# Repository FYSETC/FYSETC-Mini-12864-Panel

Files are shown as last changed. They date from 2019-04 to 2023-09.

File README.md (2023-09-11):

# Mini-12864-Panel

## Product Introduction

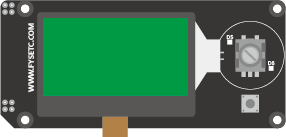
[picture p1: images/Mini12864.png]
Mini12864


这是一个便宜，带RGB指示灯，通用于marlin的显示屏，支持脱机打印，分辨率为12864，显示区域为2.4’‘，SD卡座可以为侧式或者立式，方便不同的安装场合，非常适用于小型3D打印机。

This is a opensouce, cheap, with RGB indicator, common to marlin's display, supports offline printing, resolution is 12864, display area is 2.4'', SD card holder can be side or vertical, convenient for different installation occasions Ideal for small 3D printers.

There are two versions, one with only two RGB LEDs around the encoder, the backlight is fixed color; the other one backlight is also RGB.

## Features

- 2.4" inch high contrast Graphic LCD
- Black-gray/black-green/white-black/white-blue/green-black, 5 display styles
- SPI communication to host micro-controller
- Support Vertical or side SD slot with card detect
- Rotary Encoder 
- Configurable RGB LED light
- Software configurable contrast setting
- 3D printable case and mount STL file 
- EXP1 & EXP2  RAMPS Compatible socket

## Application

3D printer，CNC machines ，Other micro controller projects

## Typical  Wiring






## 注意/NOTICE：

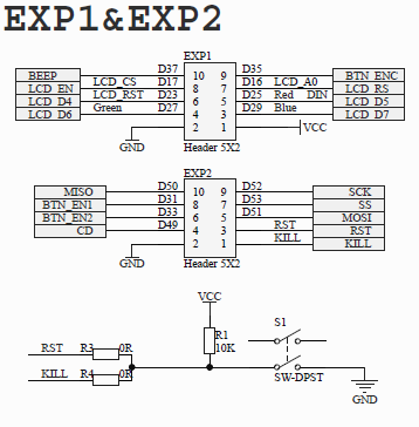
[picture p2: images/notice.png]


| Notice                                                       |
| ------------------------------------------------------------ |
| 为了兼容某些主板，如RAMPS1.4，FYSETC mini12864 设置了 RST(R3) 和 KILL(R4) 的可选择电阻。目前，有些主板（S6/Spider）将 KILL 换成 5V，此时，请确认 mini12864 上 R4处于空贴状态，否则按下屏幕上的按钮会致使 5V 与 GND 短路，长时间操作会导致主板损坏。<br/>   In order to be compatible with some motherboards, such as RAMPS1.4, mini12864 is equipped with RST (R3) and KILL (R4) optional resistors. At present, some motherboards (S6/Spider) change the KILL to 5V. At this time, please make sure that R4 on the mini12864 is in the empty state, otherwise pressing the button on the screen will cause a short circuit between 5V and GND, and long-term operation will cause the motherboard to be damaged. |

## Firmware config

### Marlin

Uncomment the following define according to your panel version, you can check it at the back of the panel.

```
//
// FYSETC variant of the MINI12864 graphic controller with SD support
// https://wiki.fysetc.com/Mini12864_Panel/
//
//#define FYSETC_MINI_12864_X_X    // Type C/D/E/F. No tunable RGB Backlight by default
//#define FYSETC_MINI_12864_1_2    // Type C/D/E/F. Simple RGB Backlight (always on)
//#define FYSETC_MINI_12864_2_0    // Type A/B. Discreet RGB Backlight
//#define FYSETC_MINI_12864_2_1  // Type A/B. Neopixel RGB Backlight
//#define FYSETC_GENERIC_12864_1_1 // Larger display with basic ON/OFF backlight.
```

### Klipper on Cheetah V3.0

```
[display]
#	mini12864 LCD Display
lcd_type: uc1701
cs_pin: PB15
a0_pin: PB12
rst_pin: PB13
encoder_pins: ^PC10,^PC11
click_pin: ^!PC6
contrast: 63
#spi_bus: spi1
spi_software_mosi_pin: PA7
spi_software_miso_pin: PA6
spi_software_sclk_pin: PA5

[neopixel fysetc_mini12864]
#	To control Neopixel RGB in mini12864 display
pin: PB14
chain_count: 3
initial_RED: 0.1
initial_GREEN: 0.5
initial_BLUE: 0.0
color_order: RGB

#	Set RGB values on boot up for each Neopixel. 
#	Index 1 = display, Index 2 and 3 = Knob
[delayed_gcode setdisplayneopixel]
initial_duration: 1
gcode:
        SET_LED LED=fysetc_mini12864 RED=1 GREEN=1 BLUE=1 INDEX=1 TRANSMIT=0
        SET_LED LED=fysetc_mini12864 RED=1 GREEN=0 BLUE=0 INDEX=2 TRANSMIT=0
        SET_LED LED=fysetc_mini12864 RED=1 GREEN=0 BLUE=0 INDEX=3 
```

## Attention

-TBD-

## FAQ

-TBD-

## Attachments
### 1. Schematic

---------

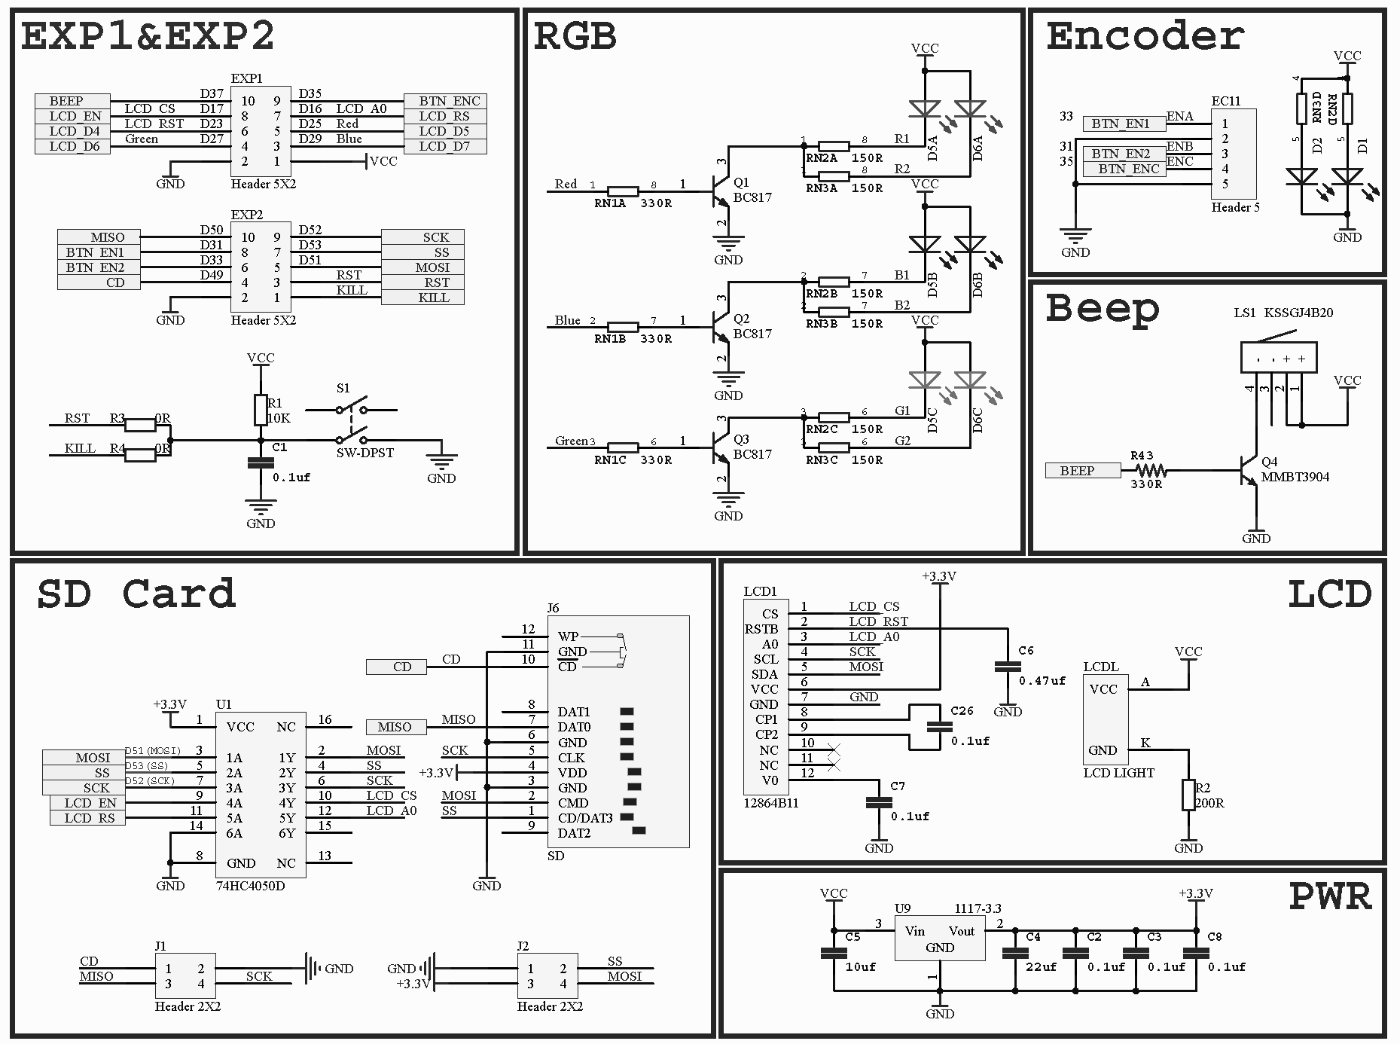
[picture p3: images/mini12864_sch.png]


### 2. Dimensions

---------

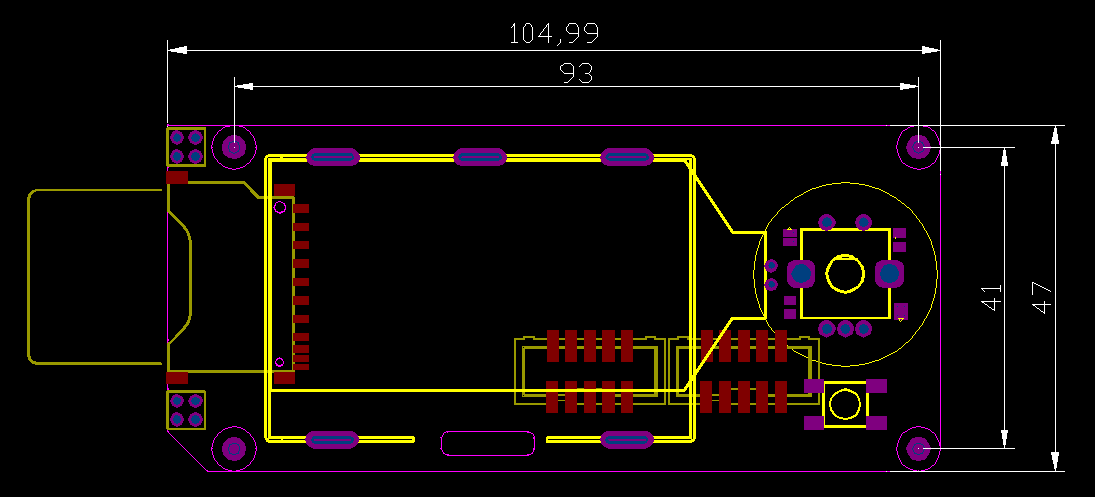
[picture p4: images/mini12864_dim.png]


**For detailed dimensions please check dwg/step file on github.**

## Shop
---
- [LCD](  )

## Tech Support
---
Please submit any technical issue into our [forum](http://forum.fysetc.com/) 

```

```

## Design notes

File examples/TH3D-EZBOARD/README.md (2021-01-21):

# FYSETC Mini 12864 Panel

FYSETC Mini 12864 Panel EXP1 and EXP2:

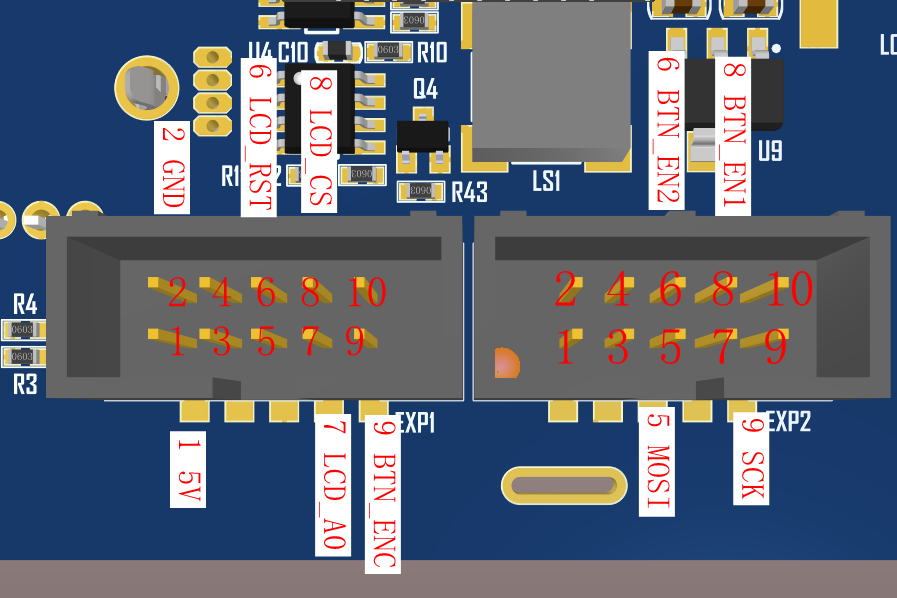
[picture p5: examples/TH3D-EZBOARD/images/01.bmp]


TH3D EZBoard EXP1:

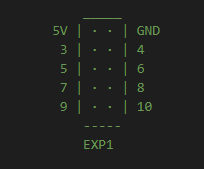
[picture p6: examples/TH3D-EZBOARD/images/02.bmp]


TH3D EZBoard only supports CR10_STOCKDISPLAY,If you want to support FYSETC Mini 12864 Panel, you need to carry out the flying line operation, so you need to prepare 10 Dupont lines, the connection operation is as follows:

| FYSETC Mini 12864 Panel EXP1 and EXP2 | TH3D EZBoard EXP1 |
| --- | --- |
| 5V | 1 |
| GND | 2 |
| LCD_CS | 3 |
| LCD_A0 | 4 |
| MOSI | 5 |
| EN2 | 6 |
| LCD_RST | 7 |
| EN1 | 8 |
| ENC | 9 |
| SCK | 10 |

## Firmware config

This firmware is only used to test mini12864, if you want to support on the latest Marlin firmware, you need to configure the following

##### Step1. changes the pins.

On a TH3D_EZBOARD board, you need to make the following changes in pins_TH3D_EZBOARD.h:

```cpp tab='pins_TH3D_EZBOARD.h'
// #if ENABLED(CR10_STOCKDISPLAY)
//   #define BEEPER_PIN                       P1_31
//   #define BTN_EN1                          P3_26
//   #define BTN_EN2                          P3_25
//   #define BTN_ENC                          P1_30
//   #define LCD_PINS_RS                      P0_16
//   #define LCD_PINS_ENABLE                  P0_18
//   #define LCD_PINS_D4                      P0_15
//   #define KILL_PIN                         P2_11
// #elif HAS_SPI_LCD
//   #error "Only the CR10_STOCKDISPLAY is supported with TH3D EZBoard."
// #endif

#if ENABLED(CR10_STOCKDISPLAY)
  #define BEEPER_PIN                       P1_31
  #define BTN_EN1                          P3_26
  #define BTN_EN2                          P3_25
  #define BTN_ENC                          P1_30
  #define LCD_PINS_RS                      P0_16
  #define LCD_PINS_ENABLE                  P0_18
  #define LCD_PINS_D4                      P0_15
  #define KILL_PIN                         P2_11
#elif ENABLED(FYSETC_MINI_12864)

  #define BTN_EN1                         P3_26
  #define BTN_EN2                         P3_25
  #define BTN_ENC                         P1_30

  #define DOGLCD_CS                       P0_18
  #define DOGLCD_A0                       P0_16
  #define DOGLCD_SCK                      P1_31
  #define DOGLCD_MOSI                     P0_15
  #define LCD_PINS_ENABLE                 P0_18
  #define LCD_PINS_RS                     P0_16

  #define FORCE_SOFT_SPI

  #define LCD_RESET_PIN                   P2_11

#elif HAS_SPI_LCD
  #error "Only the CR10_STOCKDISPLAY is supported with TH3D EZBoard."
#endif
```

##### Step2. Config the configuration.h.

Because the TH3D_EZBOARD board has only EXP1 interface, it will not be able to use the RGB function

```C++
#define FYSETC_MINI_12864_X_X    // Type C/D/E/F. No tunable RGB Backlight by default
//#define FYSETC_MINI_12864_1_2    // Type C/D/E/F. Simple RGB Backlight (always on)
//#define FYSETC_MINI_12864_2_0    // Type A/B. Discreet RGB Backlight
//#define FYSETC_MINI_12864_2_1    // Type A/B. NeoPixel RGB Backlight
//#define FYSETC_GENERIC_12864_1_1 // Larger display with basic ON/OFF backlight.
```

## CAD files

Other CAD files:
hardware/V2.1/12864mini（RGB）_V2.1.DWG
hardware/V1.2/12864mini_V1.2.DWG
hardware/V2.0/12864mini（RGB）_V2.0.DWG

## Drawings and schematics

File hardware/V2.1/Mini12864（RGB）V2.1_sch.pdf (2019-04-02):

# Encoder

EXP1&EXP2 | RGB

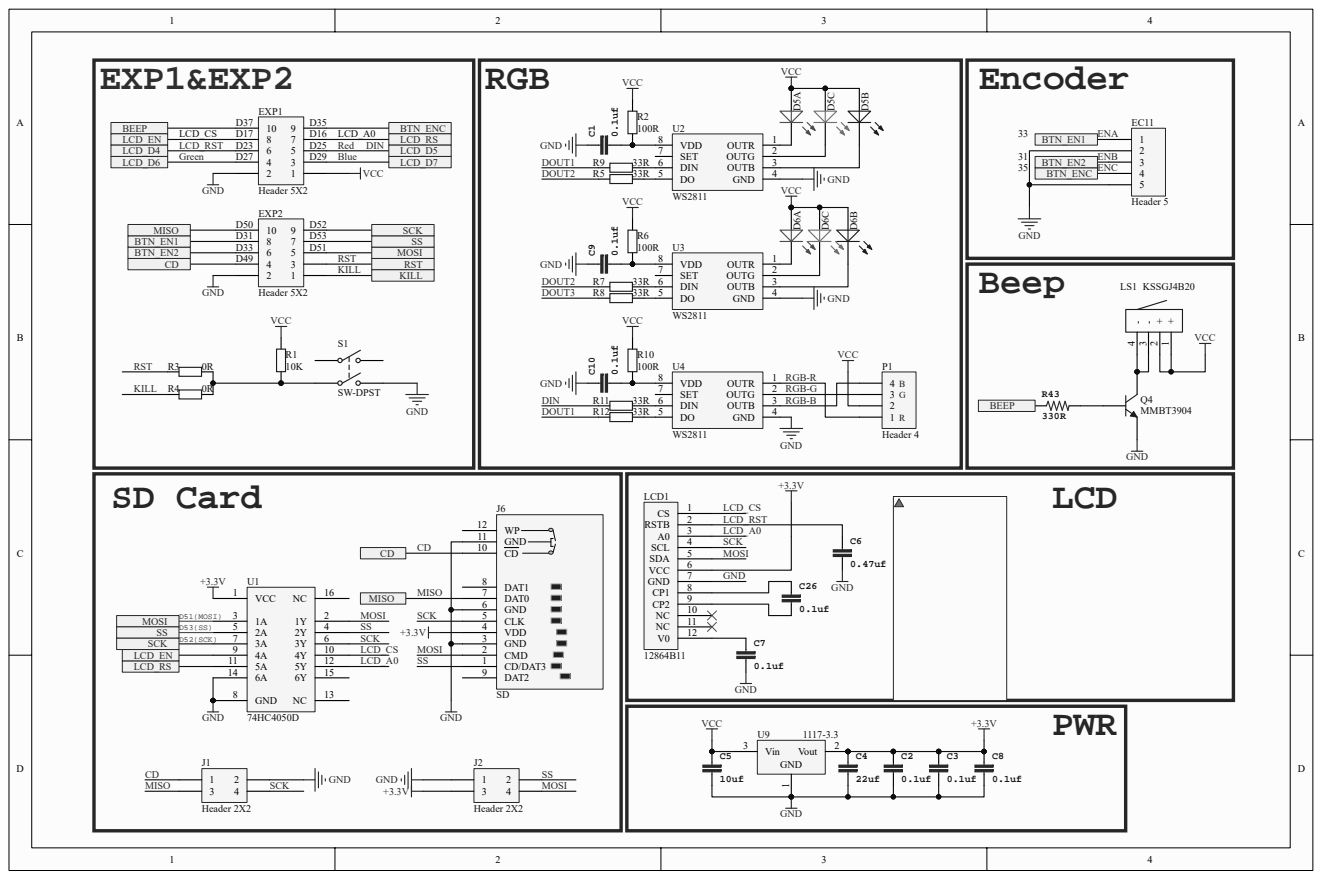
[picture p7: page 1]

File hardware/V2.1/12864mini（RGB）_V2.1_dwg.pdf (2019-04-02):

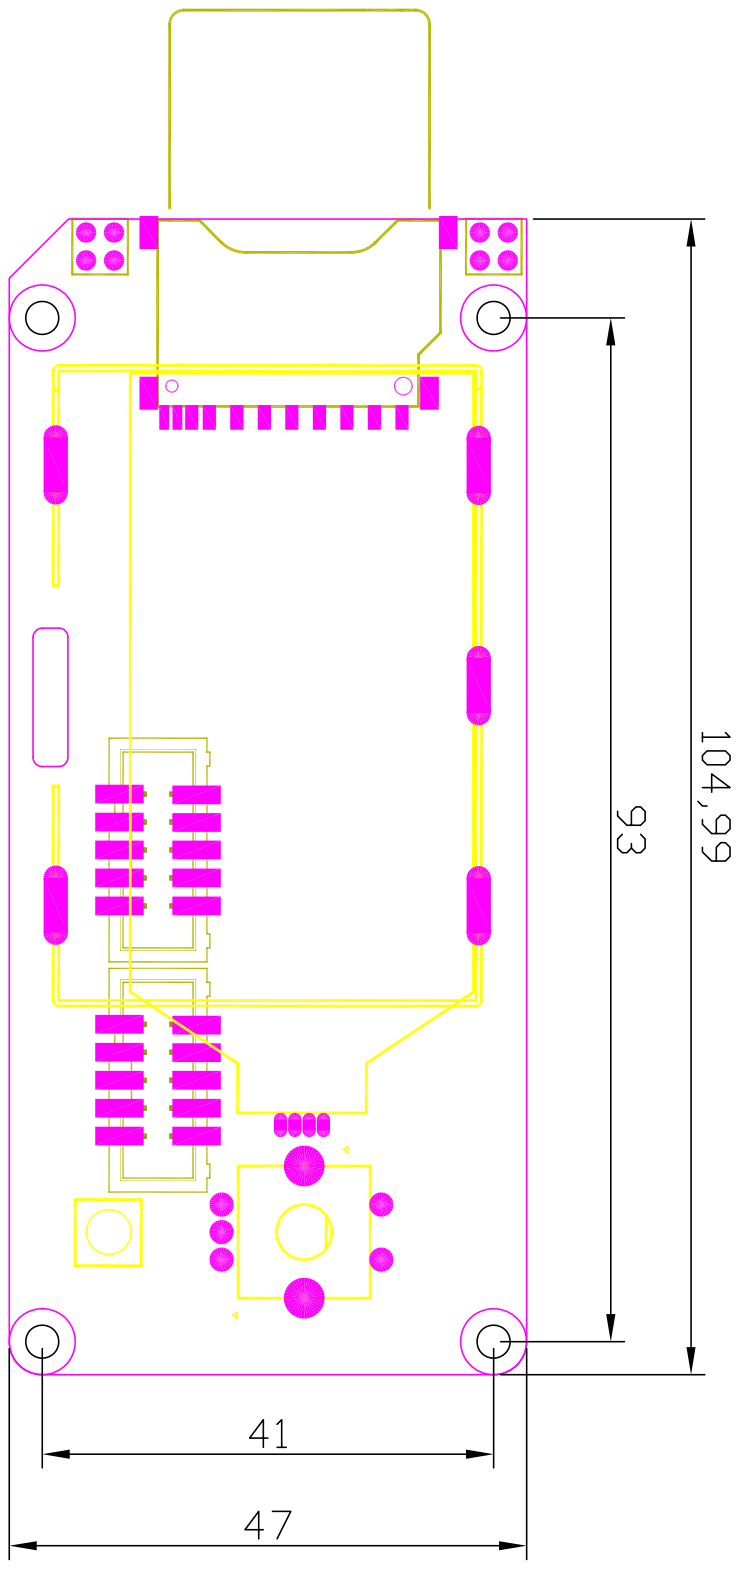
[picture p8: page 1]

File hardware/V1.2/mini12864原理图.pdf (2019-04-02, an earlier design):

# Encoder

EXP1&EXP2 | RGB

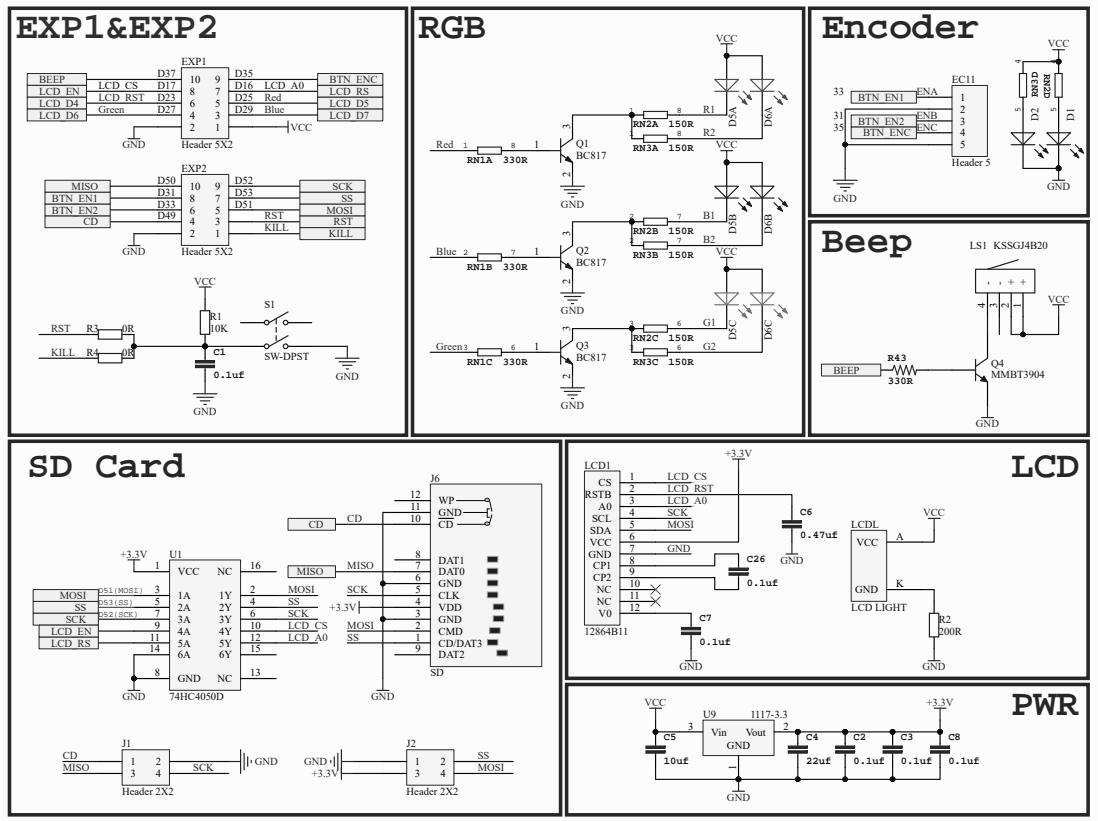
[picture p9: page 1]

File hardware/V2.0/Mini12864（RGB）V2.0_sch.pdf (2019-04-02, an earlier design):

# Encoder

EXP1&EXP2 | RGB

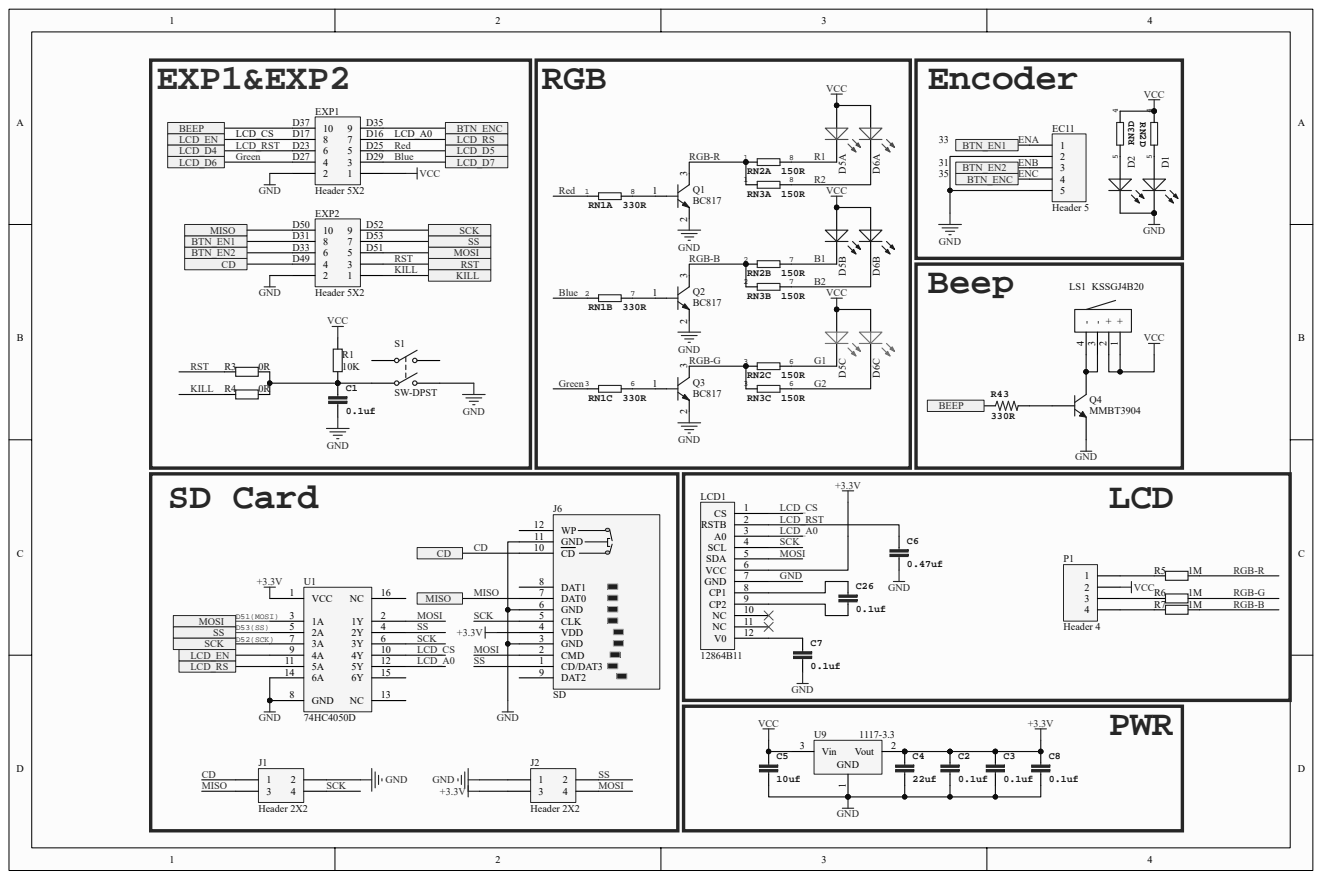
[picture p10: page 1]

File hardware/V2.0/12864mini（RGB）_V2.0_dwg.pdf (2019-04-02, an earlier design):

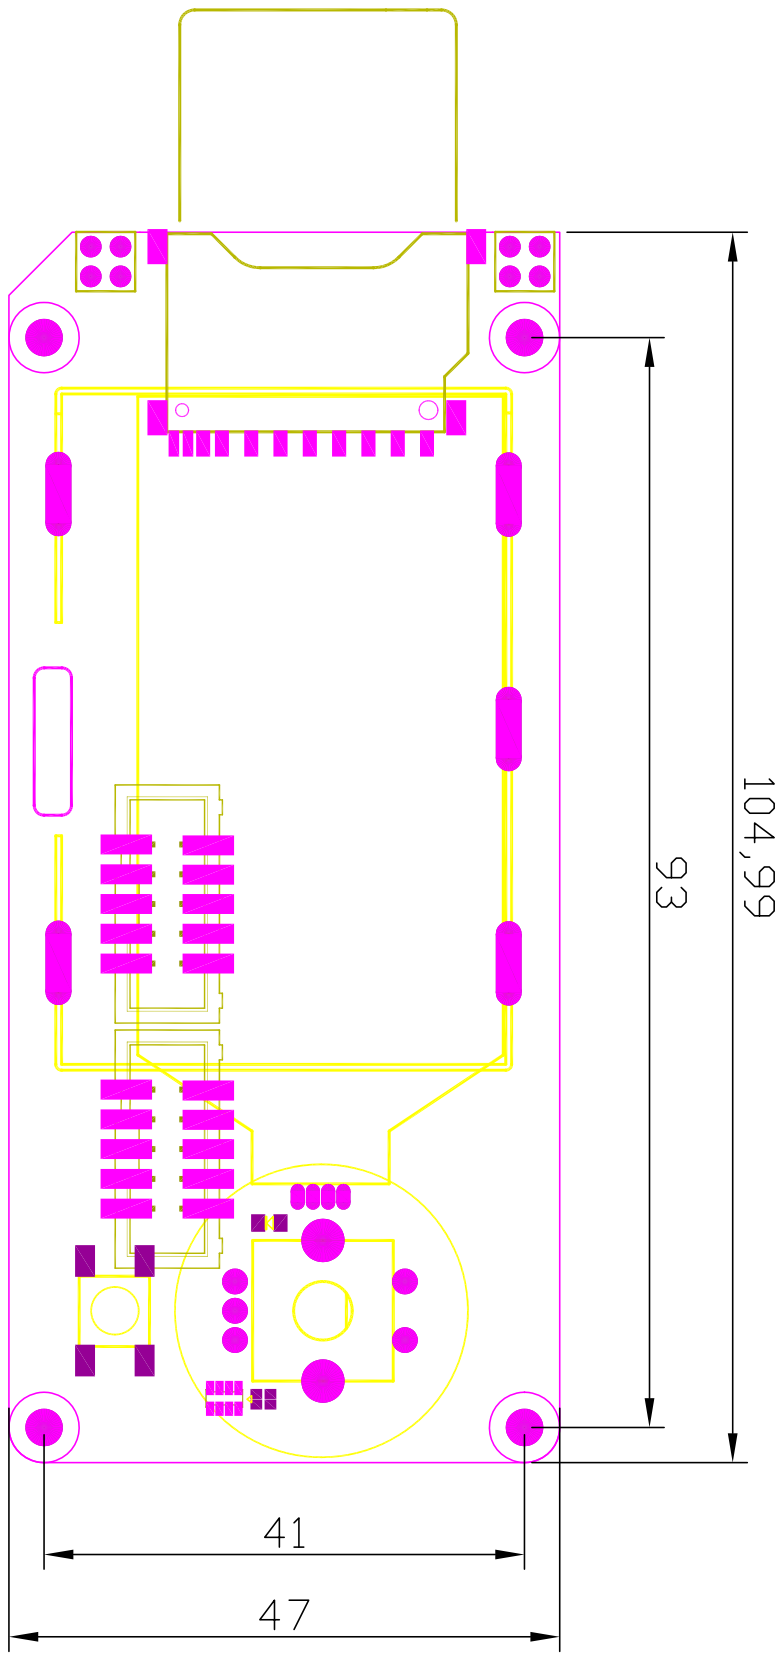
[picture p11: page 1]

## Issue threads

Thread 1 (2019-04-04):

Display does not work

Brainc0re, 2019-04-04:
I have a CR10S-Pro which normally use a touchscreen. But i didn't like and replaced it with a 12864 reprap full graphic controller. That controller/display works since weeks. So i thought, that this mini12864 will work too. But im not able to run it :/ Not even the backlight works (Pin1 and Pin2 are correct - i can meassure 5V - Pin1 (+) // Pin2 (-) and J2 has 3.3V)
I made the changes in Marlin which are provided by fysetc on their website.

Is it possible, that this display wont work on the creality mainboard?

Current Firmware (reprap 12864): https://drive.google.com/open?id=1HoQVlum-DM5lGhCuu1yqCfW6UupuqbK6
FW for mini12864: https://drive.google.com/open?id=11KdF0nT0fa-EBrvGuiYhUTILRo4qJgjR
Mainboard layout: https://drive.google.com/open?id=1Ya5zHF_WQpw7XY_BoL0zs20UwexBvtwI

Attention: Both FWs has the same *.ino name but different folder names.

ejhoness, 2021-12-17:
180º EXP1 and EXP2 in lcd,

Eugeniusz-Gienek, 2024-03-12:
> 180º EXP1 and EXP2 in lcd,

OMG that worked! Thanks man!

Closed 2024-09-19.

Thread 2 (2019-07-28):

STEP files for display are corrupted

eddietheengineer, 2019-07-28:
I am making an enclosure for this display, but the STEP files included in the Github links will not open. Can you check the files and reupload them?

Thanks!

jonathanlundstrom, 2019-09-08:
I've been at this for months and still haven't been able to use these files. The LCD mount is one of the last things on my to-do in order to finish my machine and I have not been able to design it properly. Please upload new files!

danym21, 2019-09-17:
looks like some one has changed the step files to a .zip file with a link to a
Potentially Unwanted Application (PUA)
https://www.f-secure.com/sw-desc/pua.shtml
please replace it with the correct files!!

jonathanlundstrom, 2019-09-17:
I got the correct file from a guy on their Facebook group and used it to design an enclosure for my v2.1 LCD. It worked really well and the dimensions were very accurate although there are some differences in the model of the potentiometer and the reset button, but it's all good.

I uploded it to my website so you can download it as well: [Download here](http://jonathanlundstrom.me/download/325/) :)

glabifrons, 2019-10-29:
FYSETC: The ZIP files you uploaded are not usable without installing malware. Please delete the zip files you created with KuaiZip and replace them with files created with a conventional non-proprietary ZIP program (such as InfoZip's open-source ZIP software).

Or simply upload the STEP file uncompressed, it's the same size as the zip you uploaded.

bipsendk, 2020-06-28:
Used a VM to install the PUA Zip application and extracted the STEP files for v2.0 and 2.1 - they are on https://drive.google.com/drive/folders/1SBvUNJBHfiaKfwsOxPWEyJ8HOudN6aJK?usp=sharing

wiredrat, 2021-02-21:
I don't think that forcing your customers to download a trojan is the rigth company policy.

https://www.virustotal.com/gui/file/2f187bdf55d5ff249aced33c66b4f7149e9a6972aed7bd61d15e98438ae51824/detection

3DFabrik, 2021-04-08:
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

Thanks Mate!

marcoa131, 2024-09-19:
I've deleted the .zip files for 2.0 and 2.1 and added the corresponding .step files.

marcoa131, 2024-09-20:
> > I've deleted the .zip files for 2.0 and 2.1 and added the corresponding .step files.
>
> ??? The last commit was a year ago, the zip files are still there and there are no new files.

I did the commit through github desktop, it takes a while until it updates on the web.
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

glabifrons, 2024-09-20:
> I did the commit through github desktop, it takes a while until it updates on the web. ![image]

Wow! You're not kidding that it's slow... it just showed up (4 hours later).

Thanks!

Closed 2024-09-19.

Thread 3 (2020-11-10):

Configuration update

Druckbar, 2020-11-10:
The configuration steps are outdated and misleading. Marlin 2.0.x implements the FYSETC variants natively.

There is no need to edit the `pins_RAMPS.h`.

In `configuration.h` search for **FYSETC_MINI_12864** and enable your revision of the display.

Follow the steps for your board revision and either enable **RGB_LED** (< 2.1) or **NEOPIXEL_LED** (>= 2.1).

I recommend enabling the **LED_CONTROL_MENU** in `configuration_adv.h` since you can control brightness from the LCD menu and you can set your preferred colors on startup.

Any further modifications are not neccessary. The brightness should be automatically set to 220.

I've tested the procedure with current Marlin release 2.0.7.2 on a BTT SKR 1.4 Turbo and a MKS Gen L 1.0.

YoukiNya, 2021-04-02:
I ues Marlin 2.0.7.2 on MKS SgenL 1.0
The screen can display bootscreen , but motherboard reboot again and again.
I don't know what was wrong

romass, 2021-11-11:
I have a similar problem.
LCD lights up, but no visible text appears.
Any help would be appreciated.

Board: MKS Gen L V2.1
Firmware: Marlin 2.0.9x
LCD: Fysetc Mini 12864 V2.1

configs: https://github.com/romass/3D-Printing/tree/main/MKS_gen_L_V21_Fysetc%20Mini%2012864%20V2.1%20Marlin%202

pmead7399, 2022-04-24:
If anyone is left here I need help too. I have a 2.1 and have it enabled in Marlin 2.0.1 and I get to the FINAL step which is to find the ultralcd_something_something and the file doesn't exist. Set to 220 by default? Should I be using exp 1 or 2 or both? Please help.

Obs1234, 2024-02-03:
Druckbar...Found this post. Was working on getting my BTT 12864 V2 running with no luck. Your simple how-to made my day!! Cheers from Canada, EH?

Obs1234, 2024-02-05:
Also adding this to clarify all above setting!!!

https://www.reddit.com/r/BIGTREETECH/comments/10i2ewm/fysetc_mini_12864_v21_rgb_octopus_v11_marlin_21x/

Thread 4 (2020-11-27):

Schematic for 2.1

bipsendk, 2020-11-27:
According to the description, the v2.1 display should have:

V2.1 with two RGB LEDs around the encoder, the back-light is RGB and controlled by 3 WS2811 chips, same as the NEOPIXEL_LED.

It is not clear if one or two chips are controlling the LEDs around the encoder, and the third WS2811 is controlling the backlight of the LCD.

bipsendk, 2020-11-27:
Found out by checking the PCB itself  (only because I actually had a 2.1 PCB in stock).

Closed 2020-11-27.

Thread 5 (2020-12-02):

Reset button position cannot be found on v2.1 step file, as it has not been included

bipsendk, 2020-12-02:
In the step file for v2.1 RGB  display, the reset button is not included - which makes it hard to determine the exact position.

GerogeFu, 2020-12-03:
Please refer here https://github.com/FYSETC/FYSETC-Mini-12864-Panel/issues/2

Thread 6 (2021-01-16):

TH3D-EZBOARD LITE

spankurmonkey, 2021-01-16:
Do you know how to make the Fysetc Mini 12864 to work with the TH3D-EZBOARD LITE using their unified firmware?

spankurmonkey, 2021-01-17:
You only marked 8 of the 10 pins on the TH3D EzBoard Lite set up.   I think you missed the V+ and GND

spankurmonkey, 2021-01-17:
Also TH3D has a expansion header - not sure if that would help in this situation or not.

https://www.th3dstudio.com/product/ezboard-creality-dual-lcd-adapter-board/

Also, instead of giving a bin file for the firmware it would be best to advise what to change in the firmware to make the LCD work.  That way if there is new firmware then you would not need to keep updating it.   Or you could do both, for those who want to update it just show what files, changes to make and other who do not then list the firmware and what version of it is.

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

spankurmonkey, 2021-01-19:
I tried to compile the unified firmware with your instructions in the pins file and configuration.   I get the following errors

`Compiling .pioenvs\LPC1769\src\src\lcd\menu\menu_filament.cpp.o
Compiling .pioenvs\LPC1769\src\src\lcd\menu\menu_game.cpp.o
Compiling .pioenvs\LPC1769\src\src\lcd\menu\menu_info.cpp.o
Compiling .pioenvs\LPC1769\src\src\lcd\menu\menu_main.cpp.o
Compiling .pioenvs\LPC1769\src\src\lcd\menu\menu_media.cpp.o
In file included from Marlin\src\lcd\dogm\ultralcd_DOGM.cpp:42:
Marlin\src\lcd\dogm\ultralcd_DOGM.h:60:36: error: 'LCD_PINS_ENABLE' was not declared in this scope
   60 |     #define U8G_PARAM LCD_PINS_D4, LCD_PINS_ENABLE, LCD_PINS_RS // AVR version ignores these pin settings
      |                                    ^~~~~~~~~~~~~~~
Marlin\src\lcd\dogm\ultralcd_DOGM.cpp:78:15: note: in expansion of macro 'U8G_PARAM'
   78 | U8G_CLASS u8g(U8G_PARAM);
      |               ^~~~~~~~~
Marlin\src\lcd\dogm\ultralcd_DOGM.h:60:53: error: 'LCD_PINS_RS' was not declared in this scope; did you mean 'LCD_PINS_D4'?
   60 |     #define U8G_PARAM LCD_PINS_D4, LCD_PINS_ENABLE, LCD_PINS_RS // AVR version ignores these pin settings
      |                                                     ^~~~~~~~~~~
Marlin\src\lcd\dogm\ultralcd_DOGM.cpp:78:15: note: in expansion of macro 'U8G_PARAM'
   78 | U8G_CLASS u8g(U8G_PARAM);
      |               ^~~~~~~~~
Compiling .pioenvs\LPC1769\src\src\lcd\menu\menu_mixer.cpp.o
*** [.pioenvs\LPC1769\src\src\lcd\dogm\ultralcd_DOGM.cpp.o] Error 1
=================================================================================== [FAILED] Took 41.48 seconds ===================================================================================
Environment    Status    Duration
-------------  --------  ------------
LPC1769        FAILED    00:00:41.477
============================================================================== 1 failed, 0 succeeded in 00:00:41.477 ==============================================================================The terminal process "C:\Users\kswan\.platformio\penv\Scripts\pio.exe 'run'" terminated with exit code: 1.

Terminal will be reused by tasks, press any key to close it.`

spankurmonkey, 2021-01-19:
Here is how I have the pins file attached and then in the configuration.h I have this

`//
// FYSETC variant of the MINI12864 graphic controller with SD support
// https://wiki.fysetc.com/Mini12864_Panel/
//
#define FYSETC_MINI_12864_X_X    // Type C/D/E/F. No tunable RGB Backlight by default
//#define FYSETC_MINI_12864_1_2    // Type C/D/E/F. Simple RGB Backlight (always on)
//#define FYSETC_MINI_12864_2_0    // Type A/B. Discreet RGB Backlight
//#define FYSETC_MINI_12864_2_1    // Type A/B. NeoPixel RGB Backlight
//#define FYSETC_GENERIC_12864_1_1 // Larger display with basic ON/OFF backlight.`

[pins_TH3D_EZBOARD.txt](https://github.com/FYSETC/FYSETC-Mini-12864-Panel/files/5839086/pins_TH3D_EZBOARD.txt)

spankurmonkey, 2021-01-19:
images from VScode
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

TuguanLing, 2021-01-20:
You can try to add
      #define LCD_PINS_ENABLE                 P0_18
      #define LCD_PINS_RS                     P0_16

TuguanLing, 2021-01-20:
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

spankurmonkey, 2021-01-20:
it errored again

`> Executing task: C:\Users\kswan\.platformio\penv\Scripts\pio.exe run <

Processing LPC1769 (platform: https://github.com/p3p/pio-nxplpc-arduino-lpc176x/archive/0.1.3.zip; board: nxp_lpc1769; framework: arduino)
-----------------------------------------------------------------------------------------------------------------------------------------------------------------------------------------------------------------------Verbose mode can be enabled via `-v, --verbose` option
CONFIGURATION: https://docs.platformio.org/page/boards/nxplpc-arduino-lpc176x/nxp_lpc1769.html
PLATFORM: NXP Arduino LPC176x (0.1.3) > NXP LPC1769
HARDWARE: LPC1769 120MHz, 31.97KB RAM, 464KB Flash
DEBUG: Current (cmsis-dap) On-board (cmsis-dap) External (blackmagic, jlink)
PACKAGES:
 - framework-arduino-lpc176x 0.2.5
 - toolchain-gccarmnoneeabi 1.90301.200702 (9.3.1)
Converting Marlin.ino
LDF: Library Dependency Finder -> http://bit.ly/configure-pio-ldf
LDF Modes: Finder ~ off, Compatibility ~ strict
Found 3 compatible libraries
Scanning dependencies...
Dependency Graph
|-- <Servo> 1.0.0
|-- <TMCStepper> 0.7.1
|-- <U8glib-HAL> 0.4.3
Building in release mode

Unable to find destination disk (Autodetect Error)
Please select it in platformio.ini using the upload_port keyword (https://docs.platformio.org/en/latest/projectconf/section_env_upload.html) or copy the firmware (.pio/build/LPC1769/firmware.bin) manually to the appropriate disk

Compiling .pioenvs\LPC1769\src\src\HAL\LPC1768\DebugMonitor.cpp.o
Compiling .pioenvs\LPC1769\src\src\HAL\LPC1768\HAL.cpp.o
Compiling .pioenvs\LPC1769\src\src\HAL\LPC1768\HAL_SPI.cpp.o
Compiling .pioenvs\LPC1769\src\src\HAL\LPC1768\eeprom_flash.cpp.o
Compiling .pioenvs\LPC1769\src\src\HAL\LPC1768\eeprom_sdcard.cpp.o
Compiling .pioenvs\LPC1769\src\src\HAL\LPC1768\eeprom_wired.cpp.o
Compiling .pioenvs\LPC1769\src\src\HAL\LPC1768\main.cpp.o
Compiling .pioenvs\LPC1769\src\src\HAL\LPC1768\tft\tft_spi.cpp.o
Compiling .pioenvs\LPC1769\src\src\HAL\LPC1768\tft\xpt2046.cpp.o
Compiling .pioenvs\LPC1769\src\src\HAL\LPC1768\timers.cpp.o
Compiling .pioenvs\LPC1769\src\src\HAL\LPC1768\watchdog.cpp.o
Compiling .pioenvs\LPC1769\src\src\HAL\shared\HAL_spi_L6470.cpp.o
Compiling .pioenvs\LPC1769\src\src\HAL\shared\backtrace\backtrace.cpp.o
Compiling .pioenvs\LPC1769\src\src\HAL\shared\backtrace\unwmemaccess.cpp.o
Compiling .pioenvs\LPC1769\src\src\HAL\shared\eeprom_if_i2c.cpp.o
Compiling .pioenvs\LPC1769\src\src\HAL\shared\eeprom_if_spi.cpp.o
Compiling .pioenvs\LPC1769\src\src\HAL\shared\esp_wifi.cpp.o
Compiling .pioenvs\LPC1769\src\src\HAL\shared\servo.cpp.o
Compiling .pioenvs\LPC1769\src\src\MarlinCore.cpp.o
Compiling .pioenvs\LPC1769\src\src\core\serial.cpp.o
Compiling .pioenvs\LPC1769\src\src\core\utility.cpp.o
Compiling .pioenvs\LPC1769\src\src\feature\babystep.cpp.o
Compiling .pioenvs\LPC1769\src\src\feature\bedlevel\abl\abl.cpp.o
Compiling .pioenvs\LPC1769\src\src\feature\bedlevel\bedlevel.cpp.o
Compiling .pioenvs\LPC1769\src\src\feature\controllerfan.cpp.o
Compiling .pioenvs\LPC1769\src\src\feature\pause.cpp.o
Compiling .pioenvs\LPC1769\src\src\feature\tmc_util.cpp.o
Compiling .pioenvs\LPC1769\src\src\gcode\bedlevel\G42.cpp.o
Compiling .pioenvs\LPC1769\src\src\gcode\bedlevel\M420.cpp.o
Compiling .pioenvs\LPC1769\src\src\gcode\bedlevel\abl\G29.cpp.o
Compiling .pioenvs\LPC1769\src\src\gcode\bedlevel\abl\M421.cpp.o
Compiling .pioenvs\LPC1769\src\src\gcode\calibrate\G28.cpp.o
Compiling .pioenvs\LPC1769\src\src\gcode\calibrate\M48.cpp.o
Compiling .pioenvs\LPC1769\src\src\gcode\config\M200-M205.cpp.o
Compiling .pioenvs\LPC1769\src\src\gcode\config\M220.cpp.o
Compiling .pioenvs\LPC1769\src\src\gcode\config\M221.cpp.o
Compiling .pioenvs\LPC1769\src\src\gcode\config\M301.cpp.o
Compiling .pioenvs\LPC1769\src\src\gcode\config\M302.cpp.o
Compiling .pioenvs\LPC1769\src\src\gcode\config\M92.cpp.o
Compiling .pioenvs\LPC1769\src\src\gcode\control\M108_M112_M410.cpp.o
Compiling .pioenvs\LPC1769\src\src\gcode\control\M111.cpp.o
Compiling .pioenvs\LPC1769\src\src\gcode\control\M120_M121.cpp.o
Compiling .pioenvs\LPC1769\src\src\gcode\control\M17_M18_M84.cpp.o
Compiling .pioenvs\LPC1769\src\src\gcode\control\M211.cpp.o
Compiling .pioenvs\LPC1769\src\src\gcode\control\M280.cpp.o
Compiling .pioenvs\LPC1769\src\src\gcode\control\M350_M351.cpp.o
Compiling .pioenvs\LPC1769\src\src\gcode\control\M400.cpp.o
Compiling .pioenvs\LPC1769\src\src\gcode\control\M80_M81.cpp.o
Compiling .pioenvs\LPC1769\src\src\gcode\control\M85.cpp.o
Compiling .pioenvs\LPC1769\src\src\gcode\control\M993_M994.cpp.o
Compiling .pioenvs\LPC1769\src\src\gcode\control\M997.cpp.o
Compiling .pioenvs\LPC1769\src\src\gcode\control\M999.cpp.o
Compiling .pioenvs\LPC1769\src\src\gcode\control\T.cpp.o
Compiling .pioenvs\LPC1769\src\src\gcode\eeprom\M500-M504.cpp.o
Compiling .pioenvs\LPC1769\src\src\gcode\feature\controllerfan\M710.cpp.o
Compiling .pioenvs\LPC1769\src\src\gcode\feature\digipot\M907-M910.cpp.o
Compiling .pioenvs\LPC1769\src\src\gcode\feature\pause\G27.cpp.o
Compiling .pioenvs\LPC1769\src\src\gcode\feature\pause\M125.cpp.o
Compiling .pioenvs\LPC1769\src\src\gcode\feature\pause\M600.cpp.o
Compiling .pioenvs\LPC1769\src\src\gcode\feature\pause\M603.cpp.o
Compiling .pioenvs\LPC1769\src\src\gcode\feature\trinamic\M122.cpp.o
Compiling .pioenvs\LPC1769\src\src\gcode\feature\trinamic\M569.cpp.o
Compiling .pioenvs\LPC1769\src\src\gcode\feature\trinamic\M906.cpp.o
Compiling .pioenvs\LPC1769\src\src\gcode\feature\trinamic\M911-M914.cpp.o
Compiling .pioenvs\LPC1769\src\src\gcode\gcode.cpp.o
Compiling .pioenvs\LPC1769\src\src\gcode\gcode_d.cpp.o
Compiling .pioenvs\LPC1769\src\src\gcode\geometry\G92.cpp.o
Compiling .pioenvs\LPC1769\src\src\gcode\host\M110.cpp.o
Compiling .pioenvs\LPC1769\src\src\gcode\host\M113.cpp.o
Compiling .pioenvs\LPC1769\src\src\gcode\host\M114.cpp.o
Compiling .pioenvs\LPC1769\src\src\gcode\host\M115.cpp.o
Compiling .pioenvs\LPC1769\src\src\gcode\host\M118.cpp.o
Compiling .pioenvs\LPC1769\src\src\gcode\host\M119.cpp.o
Compiling .pioenvs\LPC1769\src\src\gcode\lcd\M0_M1.cpp.o
Compiling .pioenvs\LPC1769\src\src\gcode\lcd\M117.cpp.o
Compiling .pioenvs\LPC1769\src\src\gcode\lcd\M145.cpp.o
Compiling .pioenvs\LPC1769\src\src\gcode\lcd\M300.cpp.o
Compiling .pioenvs\LPC1769\src\src\gcode\lcd\M73.cpp.o
Compiling .pioenvs\LPC1769\src\src\gcode\motion\G0_G1.cpp.o
Compiling .pioenvs\LPC1769\src\src\gcode\motion\G2_G3.cpp.o
Compiling .pioenvs\LPC1769\src\src\gcode\motion\G4.cpp.o
Compiling .pioenvs\LPC1769\src\src\gcode\motion\M290.cpp.o
Compiling .pioenvs\LPC1769\src\src\gcode\parser.cpp.o
Compiling .pioenvs\LPC1769\src\src\gcode\probe\G30.cpp.o
Compiling .pioenvs\LPC1769\src\src\gcode\probe\M401_M402.cpp.o
Compiling .pioenvs\LPC1769\src\src\gcode\probe\M851.cpp.o
Compiling .pioenvs\LPC1769\src\src\gcode\queue.cpp.o
Compiling .pioenvs\LPC1769\src\src\gcode\sd\M1001.cpp.o
Compiling .pioenvs\LPC1769\src\src\gcode\sd\M20.cpp.o
Compiling .pioenvs\LPC1769\src\src\gcode\sd\M21_M22.cpp.o
Compiling .pioenvs\LPC1769\src\src\gcode\sd\M23.cpp.o
Compiling .pioenvs\LPC1769\src\src\gcode\sd\M24_M25.cpp.o
Compiling .pioenvs\LPC1769\src\src\gcode\sd\M26.cpp.o
Compiling .pioenvs\LPC1769\src\src\gcode\sd\M27.cpp.o
Compiling .pioenvs\LPC1769\src\src\gcode\sd\M28_M29.cpp.o
Compiling .pioenvs\LPC1769\src\src\gcode\sd\M30.cpp.o
Compiling .pioenvs\LPC1769\src\src\gcode\sd\M32.cpp.o
Compiling .pioenvs\LPC1769\src\src\gcode\sd\M33.cpp.o
Compiling .pioenvs\LPC1769\src\src\gcode\sd\M34.cpp.o
Compiling .pioenvs\LPC1769\src\src\gcode\sd\M524.cpp.o
Compiling .pioenvs\LPC1769\src\src\gcode\sd\M928.cpp.o
Compiling .pioenvs\LPC1769\src\src\gcode\stats\M31.cpp.o
Compiling .pioenvs\LPC1769\src\src\gcode\stats\M75-M78.cpp.o
Compiling .pioenvs\LPC1769\src\src\gcode\temp\M104_M109.cpp.o
Compiling .pioenvs\LPC1769\src\src\gcode\temp\M105.cpp.o
Compiling .pioenvs\LPC1769\src\src\gcode\temp\M106_M107.cpp.o
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

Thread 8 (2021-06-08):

FYSETC F6 V13 AND FYSETC 12864 V2.1 NO DİSPLAY

Miran81, 2021-06-08:
Hi,
im using marlin 2.0 and fysetc f6 v1.3 and fysetc mini 12864 v2.1 lcd. When i setup marlin all is fine but screen just rgb lights on.
**NO DISPLAY**. Please help.
    #elif ENABLED(FYSETC_MINI_12864_2_1)
          #define BEEPER_PIN 37
      // Pins for DOGM SPI LCD Support

      #define LCD_BACKLIGHT_PIN -1 // backlight LED on A11/D65
      #define LCD_RESET_PIN  23
      #define SDSS   53

      #define KILL_PIN -1
      #define LCD_CONTRAST 200
      #define BTN_EN1 31
      #define BTN_EN2 33
      #define BTN_ENC 35  //the click switch

      #define SD_DETECT_PIN 49
      #define NEOPIXEL_PIN                    25
    #endif

****************************************************************************************************
//
// FYSETC variant of the MINI12864 graphic controller with SD support
// https://wiki.fysetc.com/Mini12864_Panel/
//
//#define FYSETC_MINI_12864_X_X    // Type C/D/E/F. No tunable RGB Backlight by default
//#define FYSETC_MINI_12864_1_2    // Type C/D/E/F. Simple RGB Backlight (always on)
//#define FYSETC_MINI_12864_2_0    // Type A/B. Discreet RGB Backlight
#define FYSETC_MINI_12864_2_1    // Type A/B. NeoPixel RGB Backlight
//#define FYSETC_GENERIC_12864_1_1 // Larger display with basic ON/OFF backlight.

Miran81, 2021-06-08:
@Bob-the-Kuhn

Closed 2021-06-08.

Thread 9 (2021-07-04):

Using with Arduino / ESP etc.

lukasloetkolben, 2021-07-04:
Hi i just want to use the LCD and Encoder (without the SD Card) with an Arduino Uno.
Do you have an basic wiring Example?

pommidorka, 2022-08-01:
@lukasloetkolben did you manage to connect this panel to arduino?

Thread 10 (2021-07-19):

Screen does not activate/update until click button

danbrianwhite, 2021-07-19:
When using Marlin, mks robin e3 board and a Fysetc mini display, the display does not automatically.change from the "Marlin" version screen. It gets stuck and needs a rotary button press. Then once button pressed, it goes to info screen.

Sometimes, the screen does not update after button reset pressed. And is "stuck" on previous printing screen until you press.the rotary button.

Any ideas of what is wrong or what code needs to be added to Marlin to fix this?

I can code it if I get a hint or direction front he Fysetc devs.

Best,
Dan

kjanek, 2021-07-23:
Could you send me a link to a guide how you have made this screen almost working on the mks robin e3. Because I have a MKS Robin E3D and cant figure out how to set things correctly in marlin, so that it shows text on screen (neopixel is working - i have a 2.1 version of the screen) but the screen stays blank.

mks-viva, 2021-08-10:
@danbrianwhite @kjanek
https://github.com/makerbase-mks/MKS-Robin-E3-E3D/wiki/FYSETC_BTT_MINI12864

ejhoness, 2021-12-17:
"Connect the EXP1 and EXP2 cable to the screen and to the motherboard if it still doesn't work this means you have to rotate the plug 180 degrees."

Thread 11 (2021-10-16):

FYSETC MINI 12864 NO CREALITY MOTHERBOARD CR10-S V.2.2

Yurumakum48, 2021-10-16:
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
Hello how are you? I'm having a problem with the MINI FYSETC 12864 RGB LCD board, I'm not able to configure it in Marlim at all!
I've tried it in several versions of Marlim since 1.1.9 / 1.1.x / 2.9.1 / 2.9.2 / 2.0.x but in none of them I can get it right!
The motherboard is from Creality ATMEGA 2560 V2.2.
The most I could do was make the LCD turn on all the lights, but it doesn't turn on the screen, I tried everything but nothing solved, it was a long 5 days trying, could anyone out there help me with this problem?
Attached images for further clarification.
Arduino used and the 1.8.16
Thank you all.
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

ejhoness, 2021-12-17:
Connect the EXP1 and EXP2 cable to the screen and to the motherboard if it still doesn't work this means you have to rotate the plug 180 degrees."

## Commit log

2019-04-02 add new file
    [12864mini_V1.2.DWG, 12864mini（RGB）_V2.0.DWG, 12864mini（RGB）_V2.1.DWG]
2021-01-16 Rearrange files path
    [12864mini_V1.2.DWG, 12864mini（RGB）_V2.0.DWG, 12864mini（RGB）_V2.1.DWG]
